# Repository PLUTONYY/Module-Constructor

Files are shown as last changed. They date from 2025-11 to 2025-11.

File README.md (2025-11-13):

# Module-Constructor
##  Назначение системы

Узел полезной нагрузки представляет собой модульное универсальное устройство, позволяющее решать задачи по:

- Обнаружению грузов переноски и дефектов ЛЭП;
- Переключению камер для удобства управления;
- Переноске грузов разных типов;
- Очистке ЛЭП;
- Индикации состояния.

---

## Инструкция для сборки модуля

1. Распечатайте все `.plgx` файлы на 3D-принтере.  
2. Соберите конструкцию в соответствии со схемой сборки, используя стяжки и термоклей.  
3. Проверьте конструкцию модулей на наличие жёсткой фиксации всех компонентов.  
4. Соберите электрическую часть модулей в соответствии со схемой электрических соединений.  
5. Проверьте электрическую схему на наличие короткого замыкания и правильность соединения проводов.

---

## Инструкция для развертывания системы

1. Подсоедините полётный контроллер к компьютеру.  
2. Откройте **Betaflight App** и подключитесь к дрону.  
3. Зайдите на вкладку **«Предустановки»** и выберите **«Загрузить резервную копию»**.  
4. Выберите файл `Constructor_bf.txt` и загрузите его в полётный контроллер.  
5. Подключите аппаратуру управления к компьютеру.  
6. Выберите режим **«USB Storage (SD)»**, после чего появится подключение на ПК.  
7. Откройте папку **`MODELS`** и переместите в неё файл `Constructor_rx.txt`.

---

### Примечание
Перед первым запуском рекомендуется проверить все соединения и убедиться в правильности конфигурации полётного контроллера.
ссылка на яндекс диск с презентацией и видео
https://disk.yandex.ru/d/g-EM2BR4wADh5Q

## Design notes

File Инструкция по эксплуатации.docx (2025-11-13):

# Назначение системы

Узел полезной нагрузки представляет из себя модульное универсальное устройство, позволяющее решать задачи по:

- Обнаружению грузов переноски и дефектов ЛЭП;
- Переключению камер для удобства управления;
- Переноске грузов разных типов;
- Очистке ЛЭП;
- Индикации состояния.

Инструкция для сборки модуля

1. Распечатайте все stl файлы на 3д- принетере
2. Соберите конструкцию в соответствии со схемой сборки, используя стяжки и термоклей
3. Проверите консрукцию модулей на наличие жесткой фиксации всех компонентов.
4. Соберите электрическую часть модулей в соответствии со схемой электрических соединение
5. Проверите электрическую схему на наличие короткого замыкания и правильности соединения проводов.

Инструкция для развертывания системы

1. Подсоедините полетный контроллер к компьютеру.
2. Откройте Betaflight App (https://app.betaflight.com/) и подключитесь к дрону

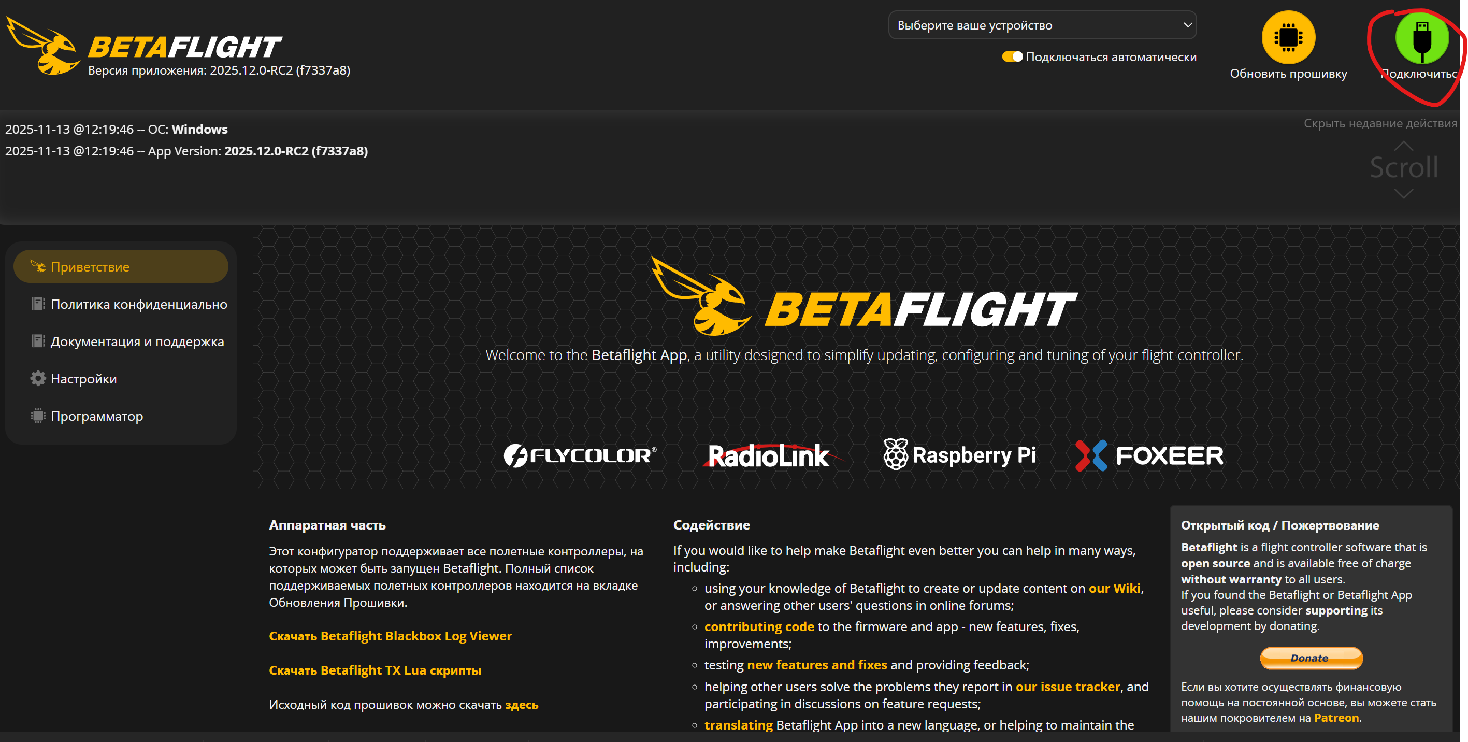
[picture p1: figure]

3. Зайдите на вкладку «Предустановки» и Выберите «Загрузить резервную копию»

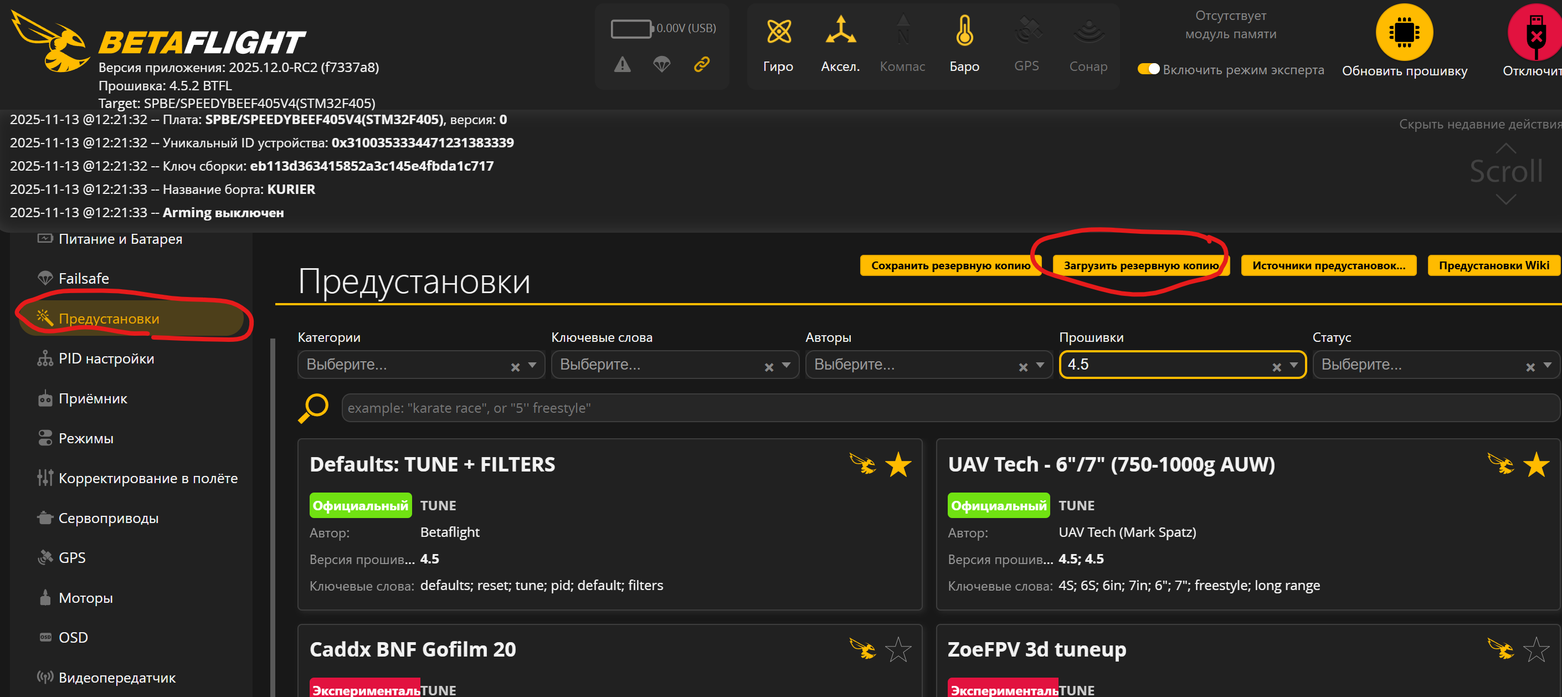
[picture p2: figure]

4. Выберите файл «Constructor_bf.txt» и загрузите в полетный контроллер
5. Подключите аппаратуру управления к компьютеру
6. Выберите режим «USB Storage (SD)» после чего появится подключение на ПК
7. Окройте папку «MODELS» и переместите в нее файл «Constructor_rx.txt»

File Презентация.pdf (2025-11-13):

# Модуль для очистки ЛЭП и переноса грузов «Консруктор»

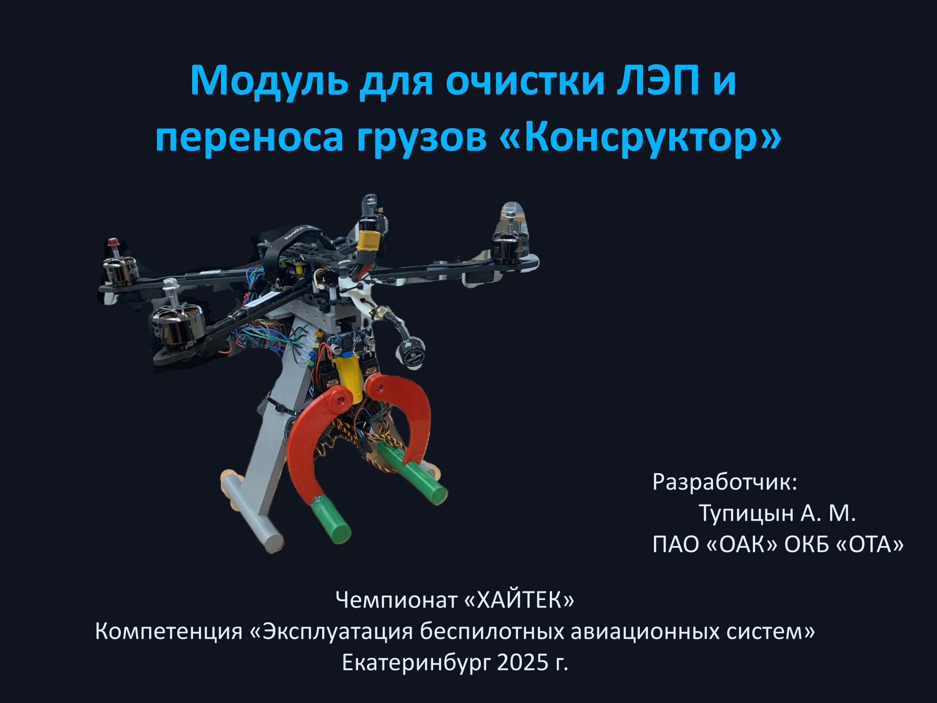
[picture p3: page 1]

Чемпионат «ХАЙТЕК»
Компетенция «Эксплуатация беспилотных авиационных систем» Екатеринбург 2025 г.

Разработчик:
Тупицын А. М.
ПАО «ОАК» ОКБ «ОТА»

# Описание модуля

Универсальный подвесной модуль для БПЛА малого класса:
- Обнаружению грузов переноски и дефектов ЛЭП;
- Переключению камер для удобства управления;
- Переноске грузов разных типов;
- Очистке ЛЭП;
- Индикации состояния.

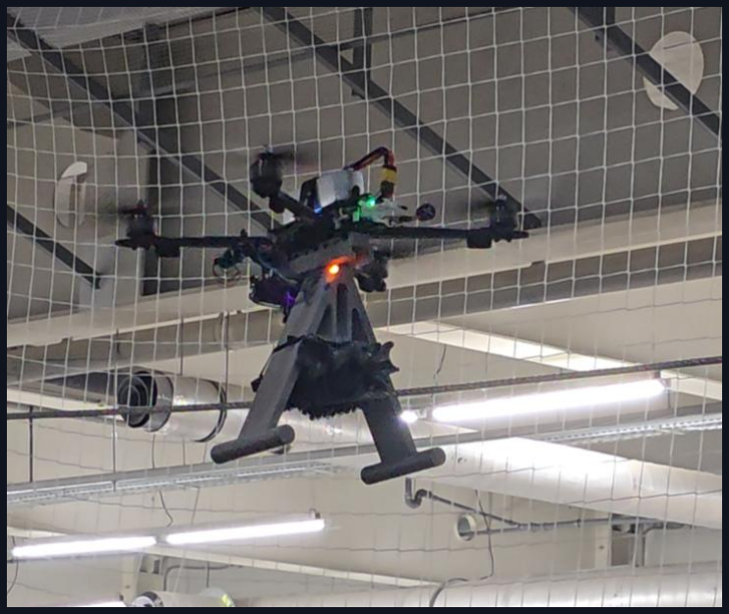
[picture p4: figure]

- Очистка ЛЭП от наледи

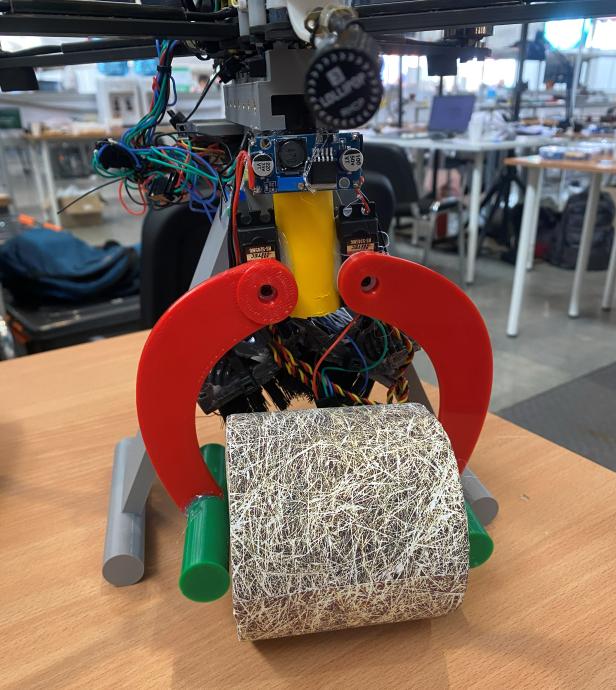
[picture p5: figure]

и загрязнений | • Перенос грузов до 500 гр

# Используемые комплектующие

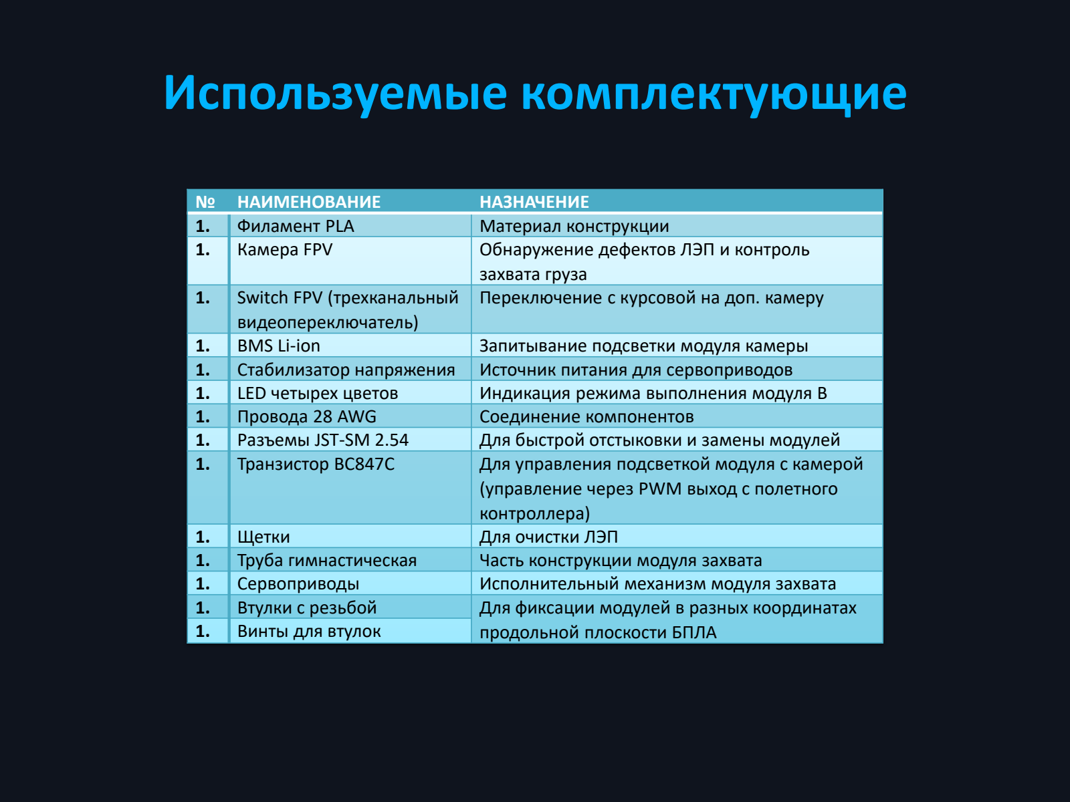
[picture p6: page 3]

№ | НАИМЕНОВАНИЕ | НАЗНАЧЕНИЕ
1. | Филамент PLA | Материал конструкции
1. | Камера FPV | Обнаружение дефектов ЛЭП и контроль захвата груза
1. Switch FPV (трехканальный | видеопереключатель) | Переключение с курсовой на доп. камеру
1. | BMS Li-ion | Запитывание подсветки модуля камеры
1. | Стабилизатор напряжения | Источник питания для сервоприводов
1. | LED четырех цветов | Индикация режима выполнения модуля B
1. | Провода 28 AWG | Соединение компонентов
1. | Разъемы JST-SM 2.54 | Для быстрой отстыковки и замены модулей
1. | Транзистор BC847C | Для управления подсветкой модуля с камерой (управление через PWM выход с полетного контроллера)
1. | Щетки | Для очистки ЛЭП
1. | Труба гимнастическая | Часть конструкции модуля захвата
1. | Сервоприводы | Исполнительный механизм модуля захвата
1. | Втулки с резьбой | Для фиксации модулей в разных координатах продольной плоскости БПЛА
1. | Винты для втулок

# Испытания по переносу грузов

- БПЛА: грузоподъёмность 800 г
- Груз: до 500 г
Итог: БПЛА не взлетел из-за технических неполадок

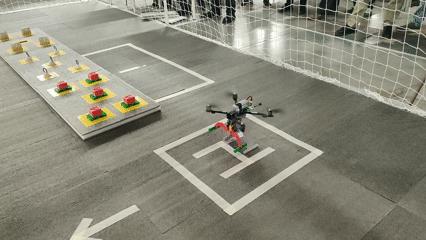
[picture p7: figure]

# Испытания по очистке ЛЭП

- Участок: ЛЭП 20м
- Эффективность очистки: 20%
- Время 100 м линии: 10 мин
Итог:
- Зачистка одного участка загрязнений
- Крушение из-за столкновением с проводом

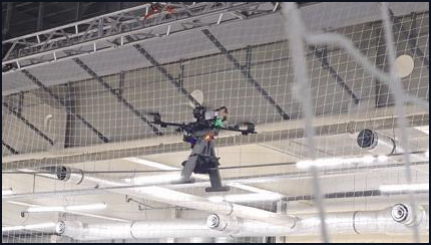
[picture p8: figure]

# Экономическое обоснование

Себестоимость:
- Модуль: 10 000₽
- БПЛА : 100 000₽
Затраты на вылет:
- Оплата услуг оператора БПЛА: 100 000₽
- Запасные комплектующие: 5 000₽ Прибыль:
- Очистка 1 км ЛЭП вручную: 250 000 ₽ Окупаемость ~ 2 месяца

Преимущества разработки:
- Снижение затрат и рисков
- Повышение безопасности работ
- Быстрое развертывание
- Модульная совместимость с разными БПЛА

# Перспективы развития

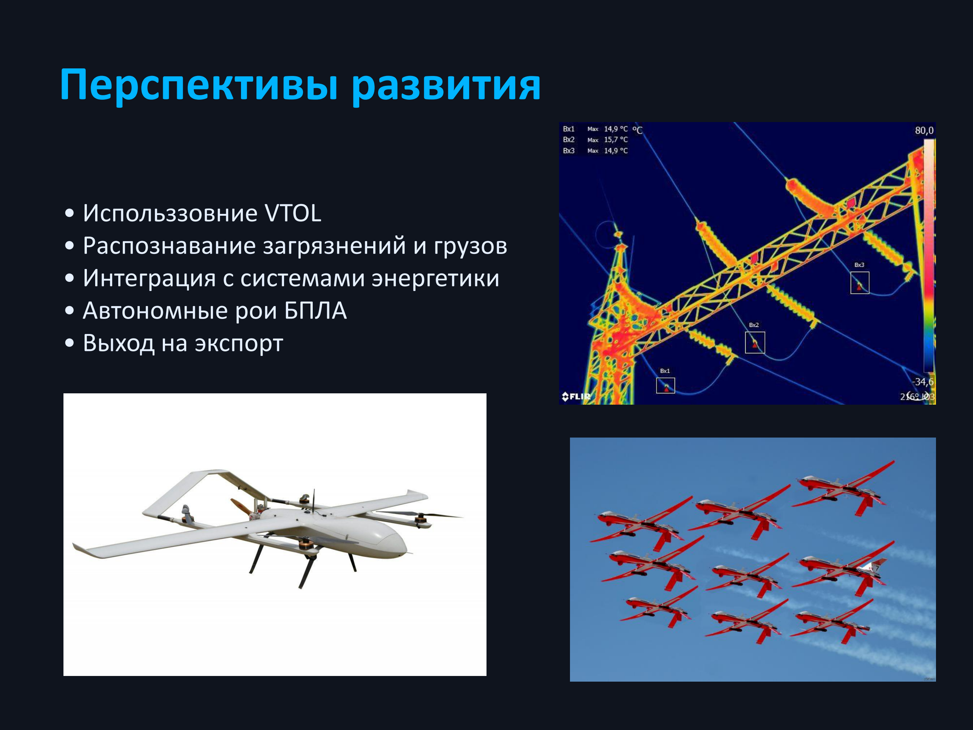
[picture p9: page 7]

- Использзовние VTOL
- Распознавание загрязнений и грузов
- Интеграция с системами энергетики
- Автономные рои БПЛА
- Выход на экспорт

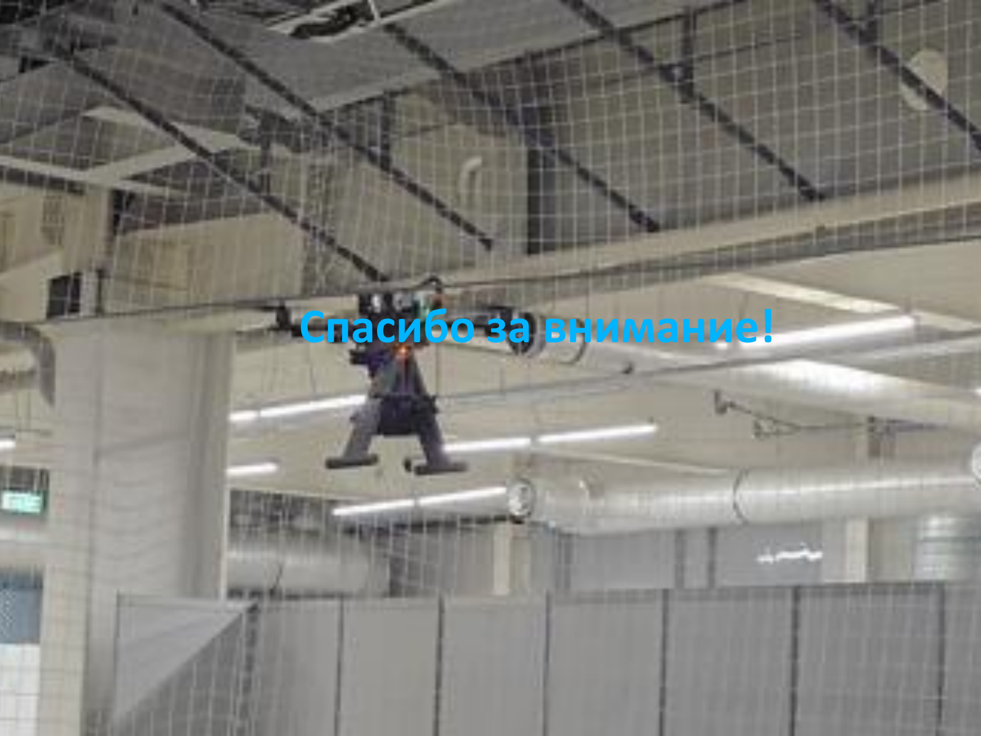
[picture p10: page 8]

# Спасибо за внимание!

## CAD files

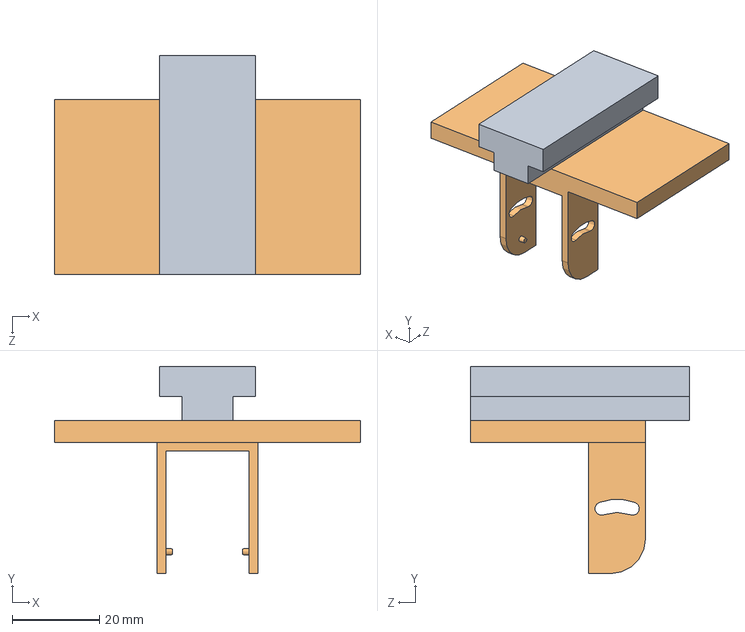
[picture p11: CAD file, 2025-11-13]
Модель сборки/Assem Cam.SLDASM
70.0 x 47.4 x 50.0 mm
inner rail for wire checker
Cam bracket

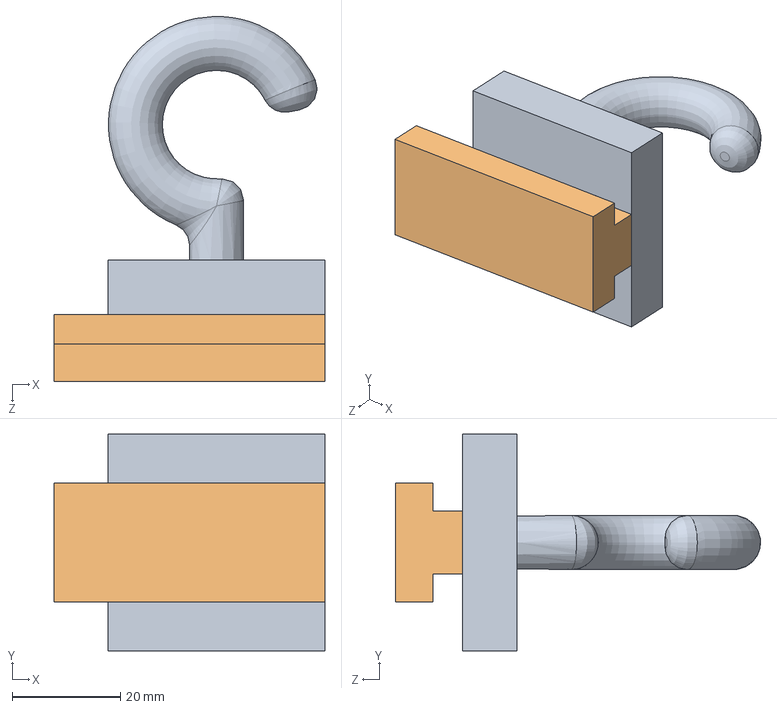
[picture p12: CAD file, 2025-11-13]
Модель сборки/Assem Hook.SLDASM
50.0 x 40.0 x 67.3 mm
Hook
inner rail for wire checker

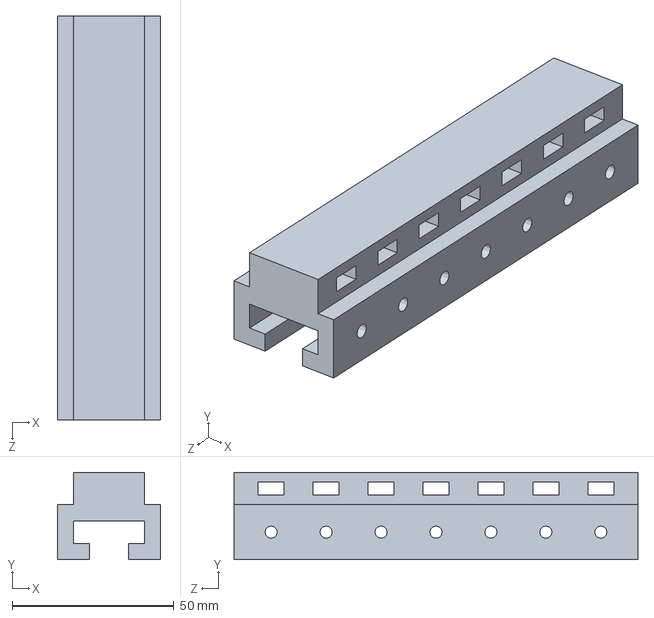
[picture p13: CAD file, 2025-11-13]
Модель сборки/Main rail_clear.SLDPRT
32.0 x 27.0 x 125.0 mm

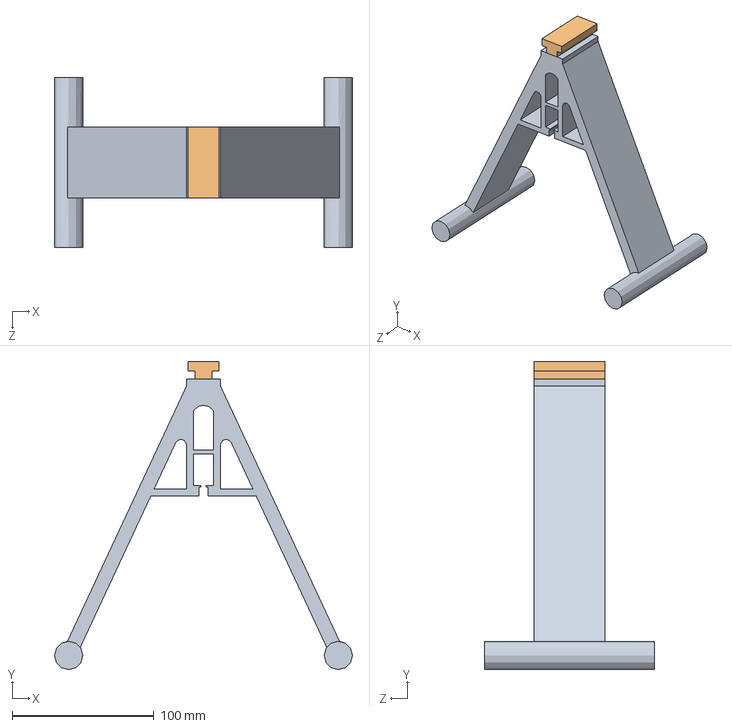
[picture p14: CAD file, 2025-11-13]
Модель сборки/Assem Wire Checker.SLDASM
210.2 x 217.4 x 120.0 mm
Wire Checker
inner rail for wire checker

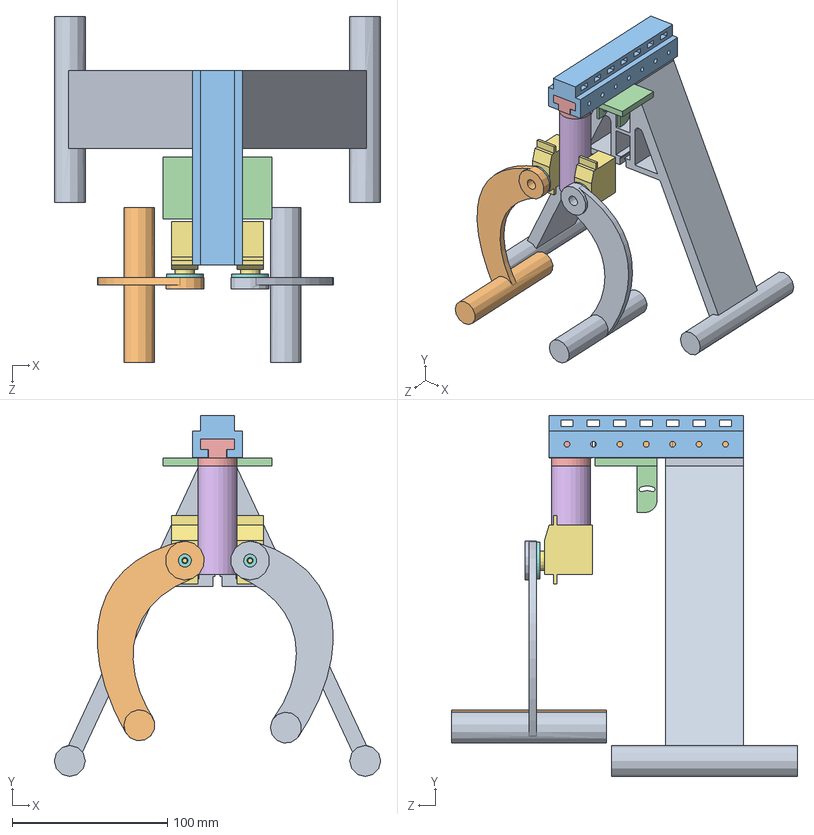
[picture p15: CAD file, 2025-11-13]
Модель сборки/Assem claw.SLDASM
210.2 x 232.4 x 223.0 mm
Wire Checker
inner rail for wire checker x 2
Main rail_clear
Cam bracket
Top of catcher
tube
Servo x 2
Servo's disk x 2
Claw_Mirrored
Claw

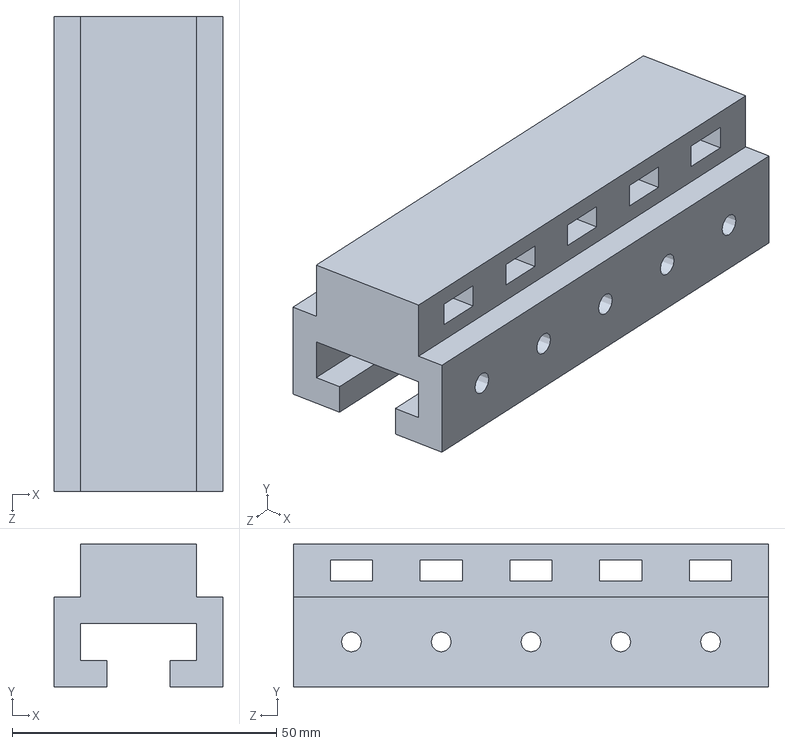
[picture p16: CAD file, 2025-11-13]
Модель сборки/Main rail.SLDPRT
32.0 x 27.0 x 90.0 mm

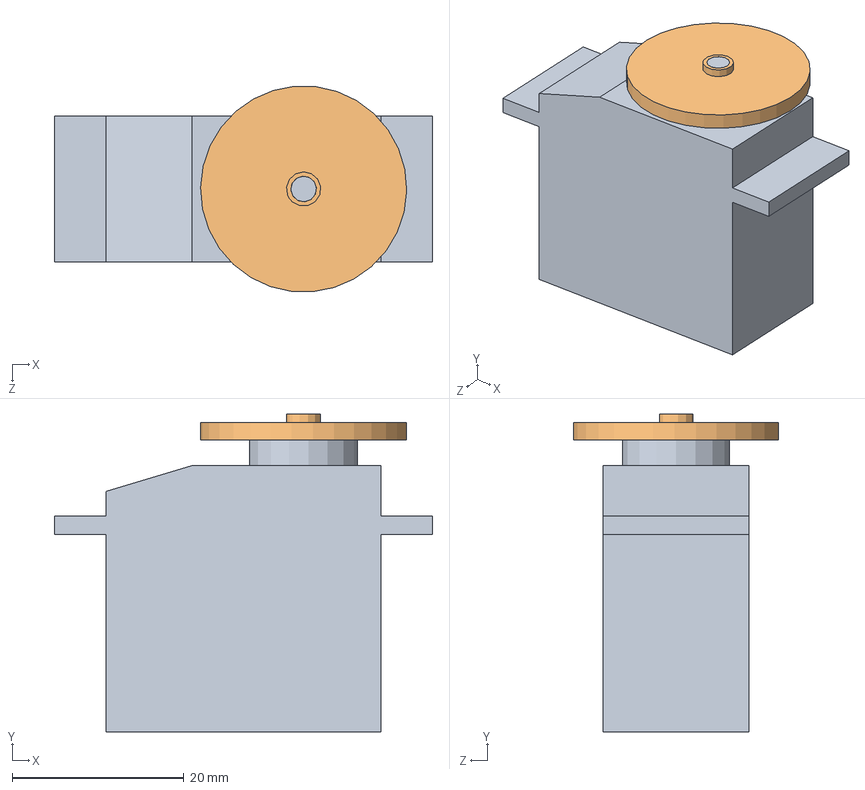
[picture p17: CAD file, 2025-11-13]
Модель сборки/Servo_assem.SLDASM
44.0 x 37.0 x 23.9 mm
Servo
Servo's disk

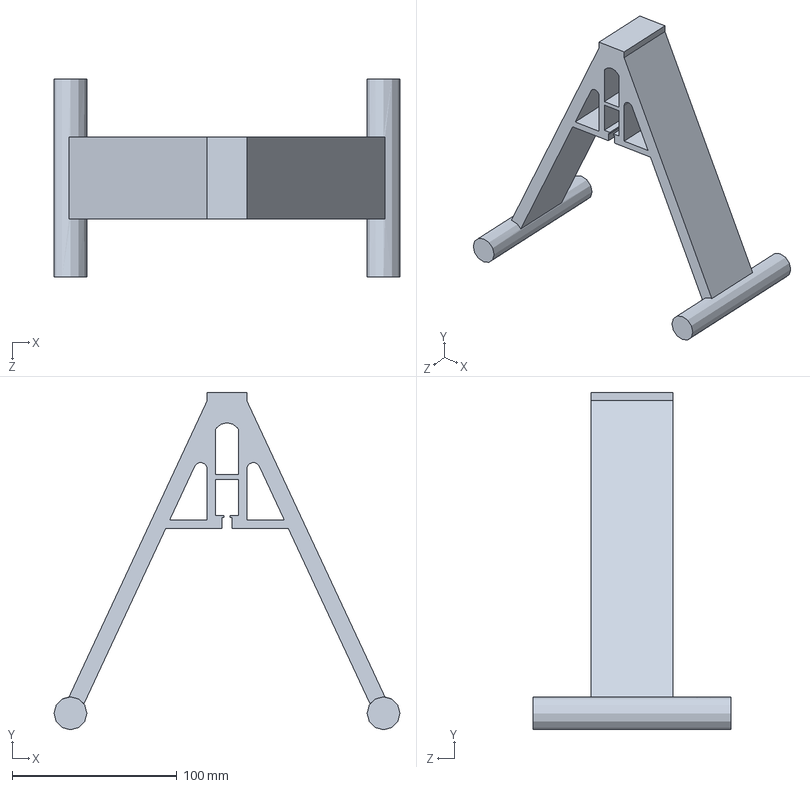
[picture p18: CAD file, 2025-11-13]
Модель сборки/Wire Checker.SLDPRT
210.2 x 205.0 x 120.0 mm

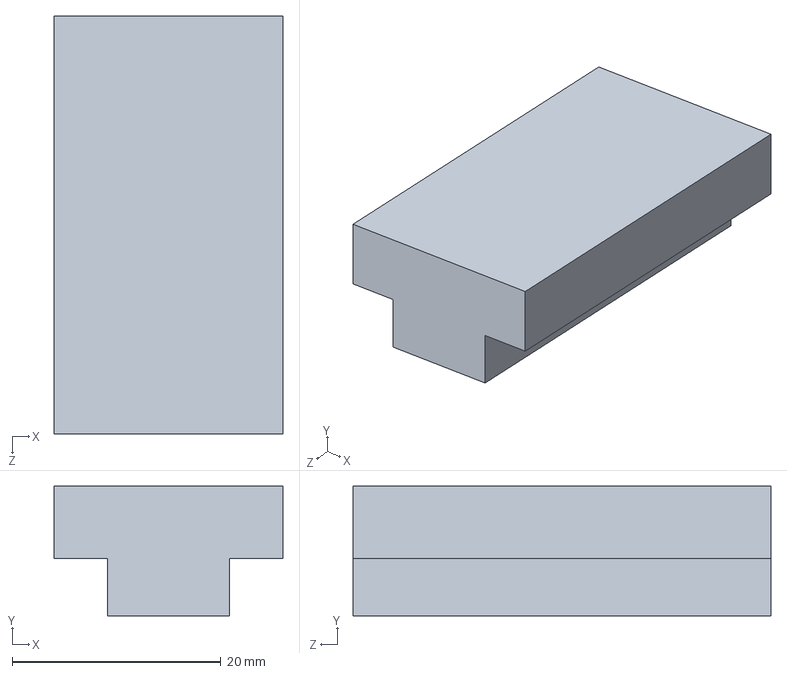
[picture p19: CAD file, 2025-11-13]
Модель сборки/inner rail test.SLDPRT
21.9 x 12.4 x 40.0 mm

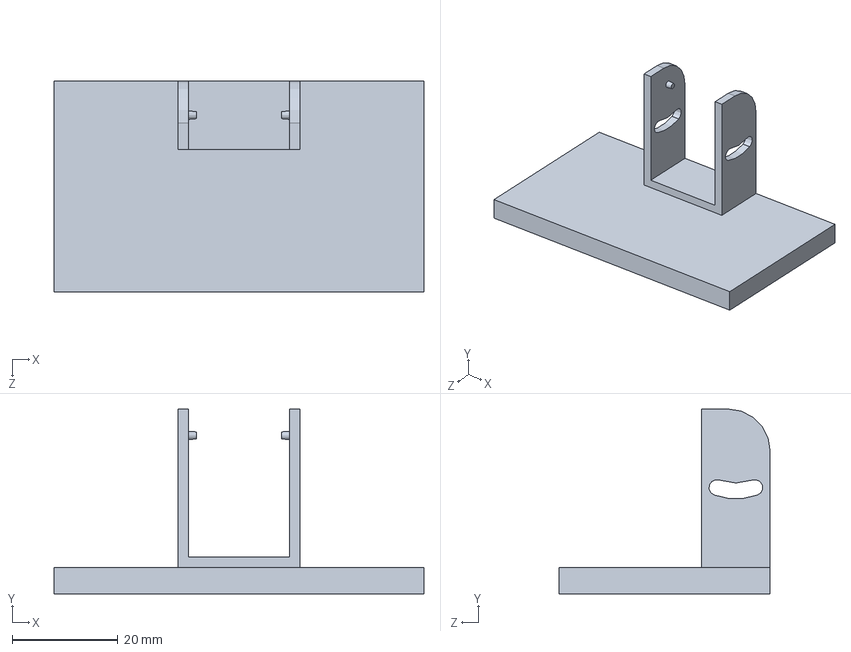
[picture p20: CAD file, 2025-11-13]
Модель сборки/Cam bracket.SLDPRT
70.0 x 35.0 x 40.0 mm

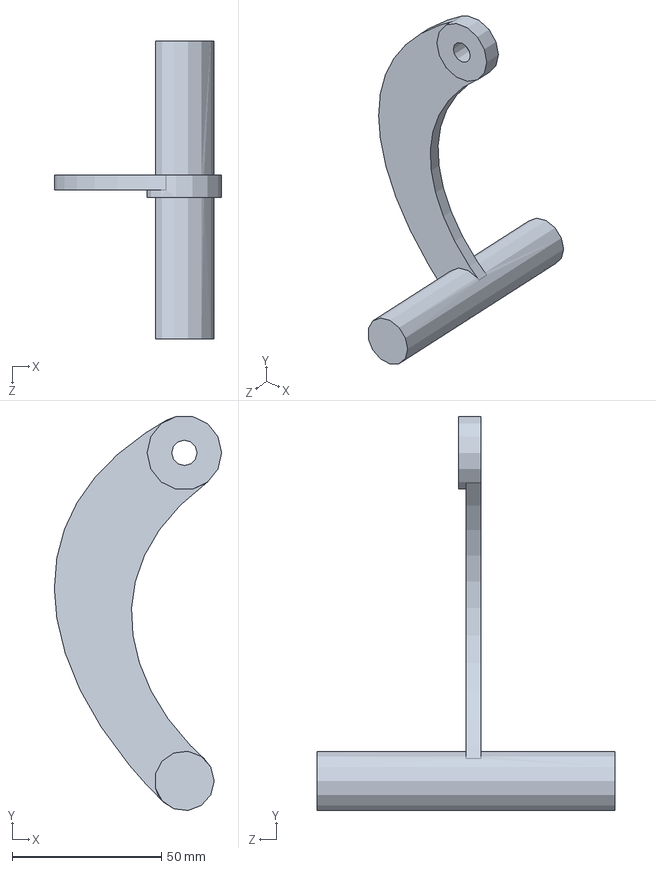
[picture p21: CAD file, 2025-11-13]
Модель сборки/Claw.SLDPRT
56.1 x 132.1 x 100.0 mm

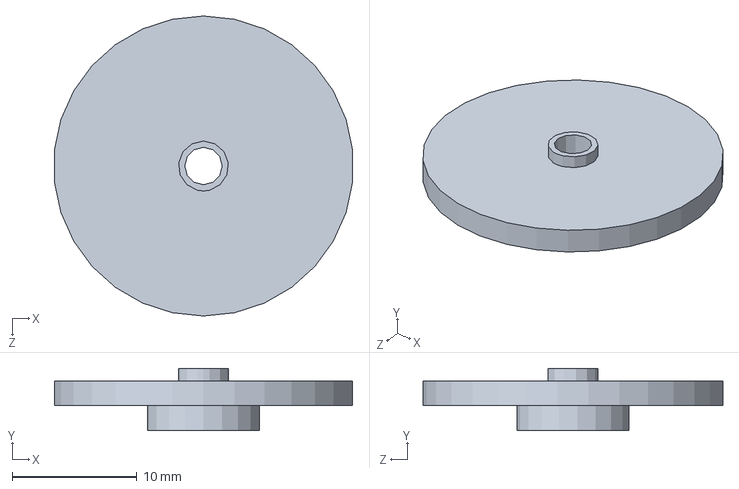
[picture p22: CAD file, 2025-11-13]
Модель сборки/Servo's disk.SLDPRT
23.9 x 5.00 x 24.0 mm

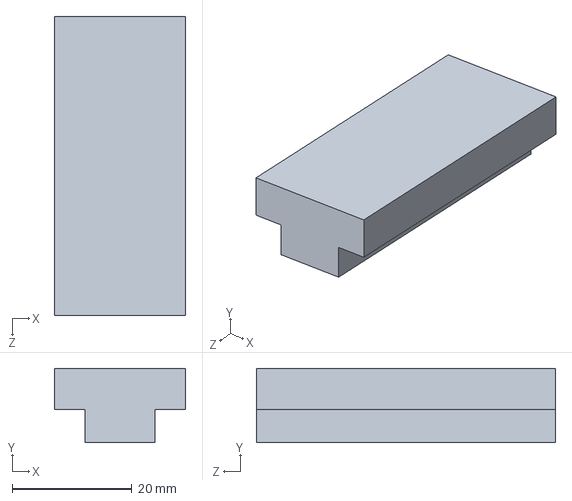
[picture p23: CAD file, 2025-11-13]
Модель сборки/inner rail for wire checker.SLDPRT
21.9 x 12.4 x 50.0 mm

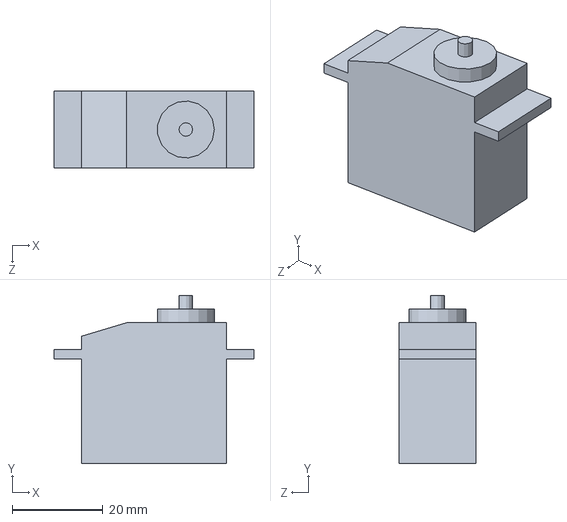
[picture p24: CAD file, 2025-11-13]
Модель сборки/Servo.SLDPRT
44.0 x 37.0 x 17.0 mm

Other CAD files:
Чертежи/AUTOCAD/Общий вид.dwg
Чертежи/AUTOCAD/Структурная схема.dwg
Модель сборки/Part1.SLDPRT
Модель сборки/Top of catcher.SLDPRT
Модель сборки/Assem claw/Assem claw/Assem Cam.iam
Модель сборки/Assem claw/Assem claw/Assem Wire Checker.iam
Модель сборки/Assem claw/Assem claw/Assem claw.iam
Модель сборки/Assem claw/Assem claw/Cam bracket.ipt
Модель сборки/Assem claw/Assem claw/Claw.ipt
Модель сборки/Assem claw/Assem claw/Claw_Mirrored.ipt
Модель сборки/Assem claw/Assem claw/Main rail_clear.ipt
Модель сборки/Assem claw/Assem claw/Servo's disk.ipt
Модель сборки/Assem claw/Assem claw/Servo.ipt
Модель сборки/Assem claw/Assem claw/Servo_assem.iam
Модель сборки/Assem claw/Assem claw/Top of catcher.ipt
Модель сборки/Assem claw/Assem claw/Wire Checker.ipt
Модель сборки/Assem claw/Assem claw/inner rail for wire checker.ipt
Модель сборки/Assem claw/Assem claw/tube.ipt
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

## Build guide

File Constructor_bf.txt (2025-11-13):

defaults nosave

# version
# Betaflight / STM32F405 (S405) 4.5.2 Nov  9 2025 / 13:51:33 (024f8e13d) MSP API: 1.46
# config rev: a3507b7

# start the command batch
batch start

# reset configuration to default settings
defaults nosave

board_name SPEEDYBEEF405V4
manufacturer_id SPBE
mcu_id 0039001e3133471834333035
signature 

# resources
resource MOTOR 5 NONE
resource MOTOR 6 NONE
resource MOTOR 7 NONE
resource MOTOR 8 NONE
resource SERVO 1 B10
resource SERVO 2 A15
resource SERVO 3 C08
resource SERVO 4 C09
resource SERIAL_TX 6 NONE
resource SERIAL_RX 1 NONE
resource SERIAL_RX 6 NONE
resource PINIO 1 A10
resource PINIO 2 C07
resource PINIO 3 C06

# feature
feature SERVO_TILT
feature TELEMETRY
feature LED_STRIP
feature DISPLAY
feature OSD
feature CHANNEL_FORWARDING

# master
set osd_canvas_height = 13
set pinio_config = 129,129,129,129
set pinio_box = 40,41,42,43

profile 0

profile 1

profile 2

profile 3

# restore original profile selection
profile 0

rateprofile 0

rateprofile 1

rateprofile 2

rateprofile 3

# restore original rateprofile selection
rateprofile 0

# save configuration

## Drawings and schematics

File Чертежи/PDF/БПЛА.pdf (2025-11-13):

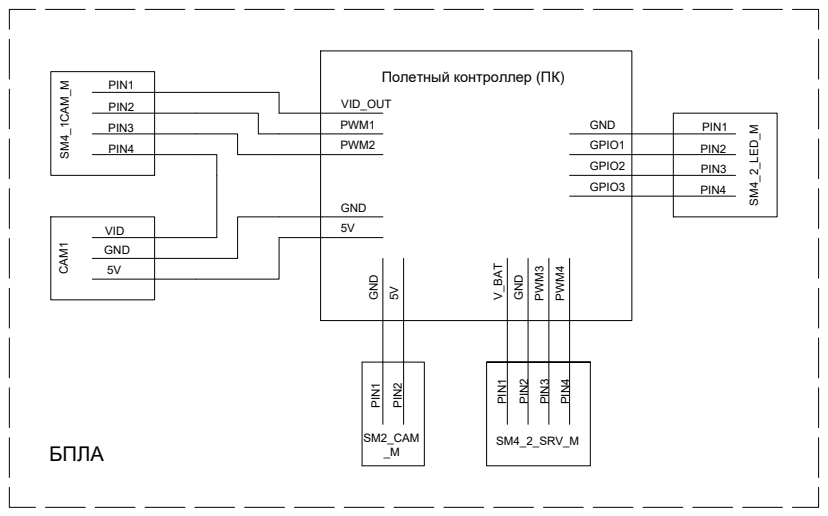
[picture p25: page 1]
PWM4 GND GPIO1 GPIO2 GPIO3; 5V PIN2 PIN3 PIN4 PIN1; PIN4 PIN2 PIN3 PIN4 PIN1 SM4_2_LED_M SM2_CAM SM4_2_SRV_M _M GND 5V; CAM1 БПЛАGND 5VVID

Полетный контроллер (ПК) VID_OUT PWM1 PWM2

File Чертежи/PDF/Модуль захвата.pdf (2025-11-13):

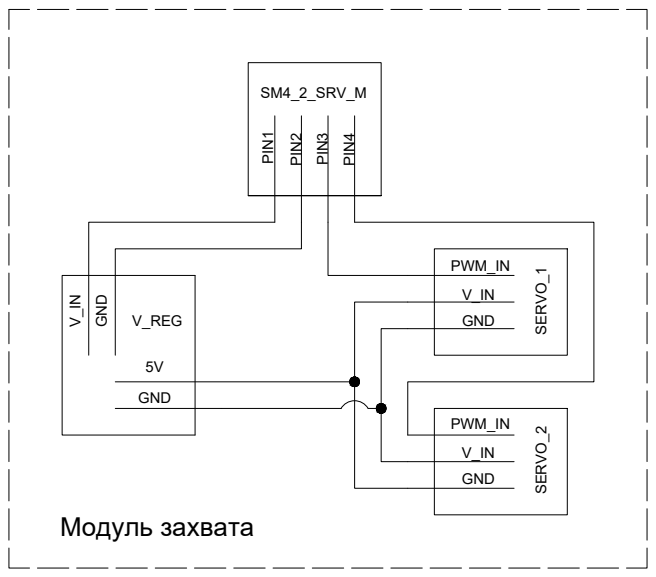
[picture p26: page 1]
PIN4 SM4_2_SRV_M; SERVO_1 SERVO_2 V_REG V_IN GND PWM_IN GND 5V

GND V_IN GND PWM_IN Модуль захвата

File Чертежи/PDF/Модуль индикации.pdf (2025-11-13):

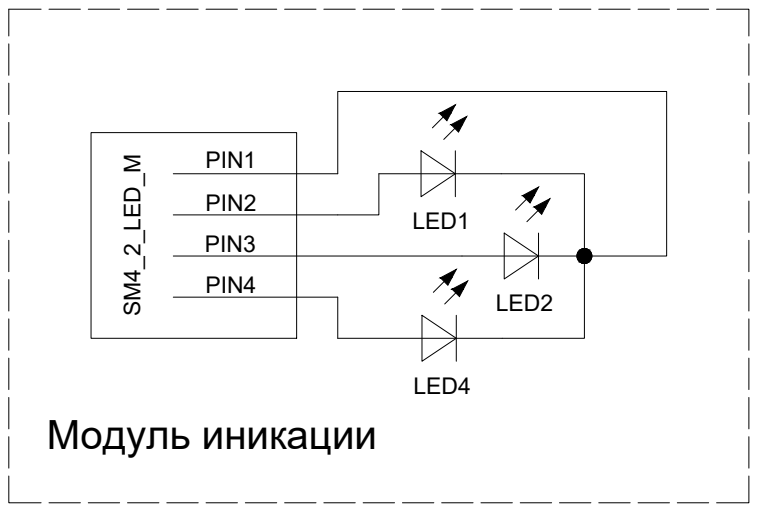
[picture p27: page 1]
PIN2 PIN3 PIN4 PIN1 SM4_2_LED_M LED1 LED2 LED4 Модуль иникации

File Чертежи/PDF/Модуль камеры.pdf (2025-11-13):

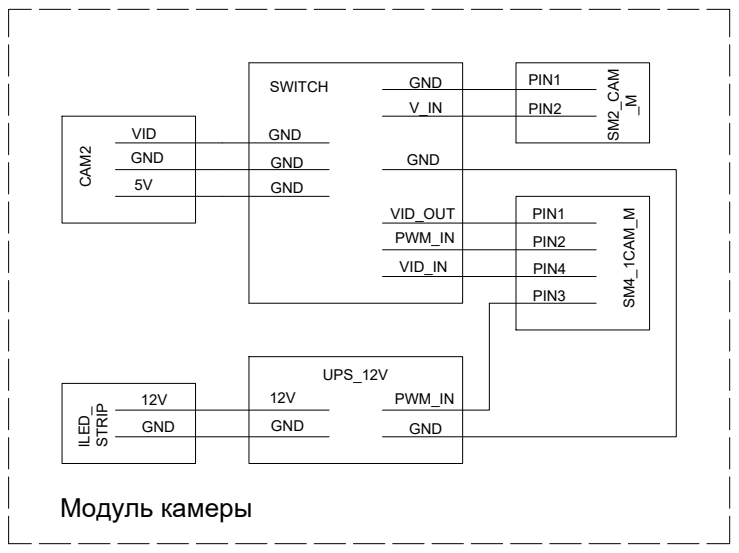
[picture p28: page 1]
PIN2 PIN1 _M PIN2 PIN4 PIN3 PIN1; SM4_1CAM_M SWITCH; CAM2GND 5VVID UPS_12V

STRIP12V GND 12V GND PWM_IN GND GND GND GND V_IN VID_OUT PWM_IN VID_IN GND GND Модуль камеры

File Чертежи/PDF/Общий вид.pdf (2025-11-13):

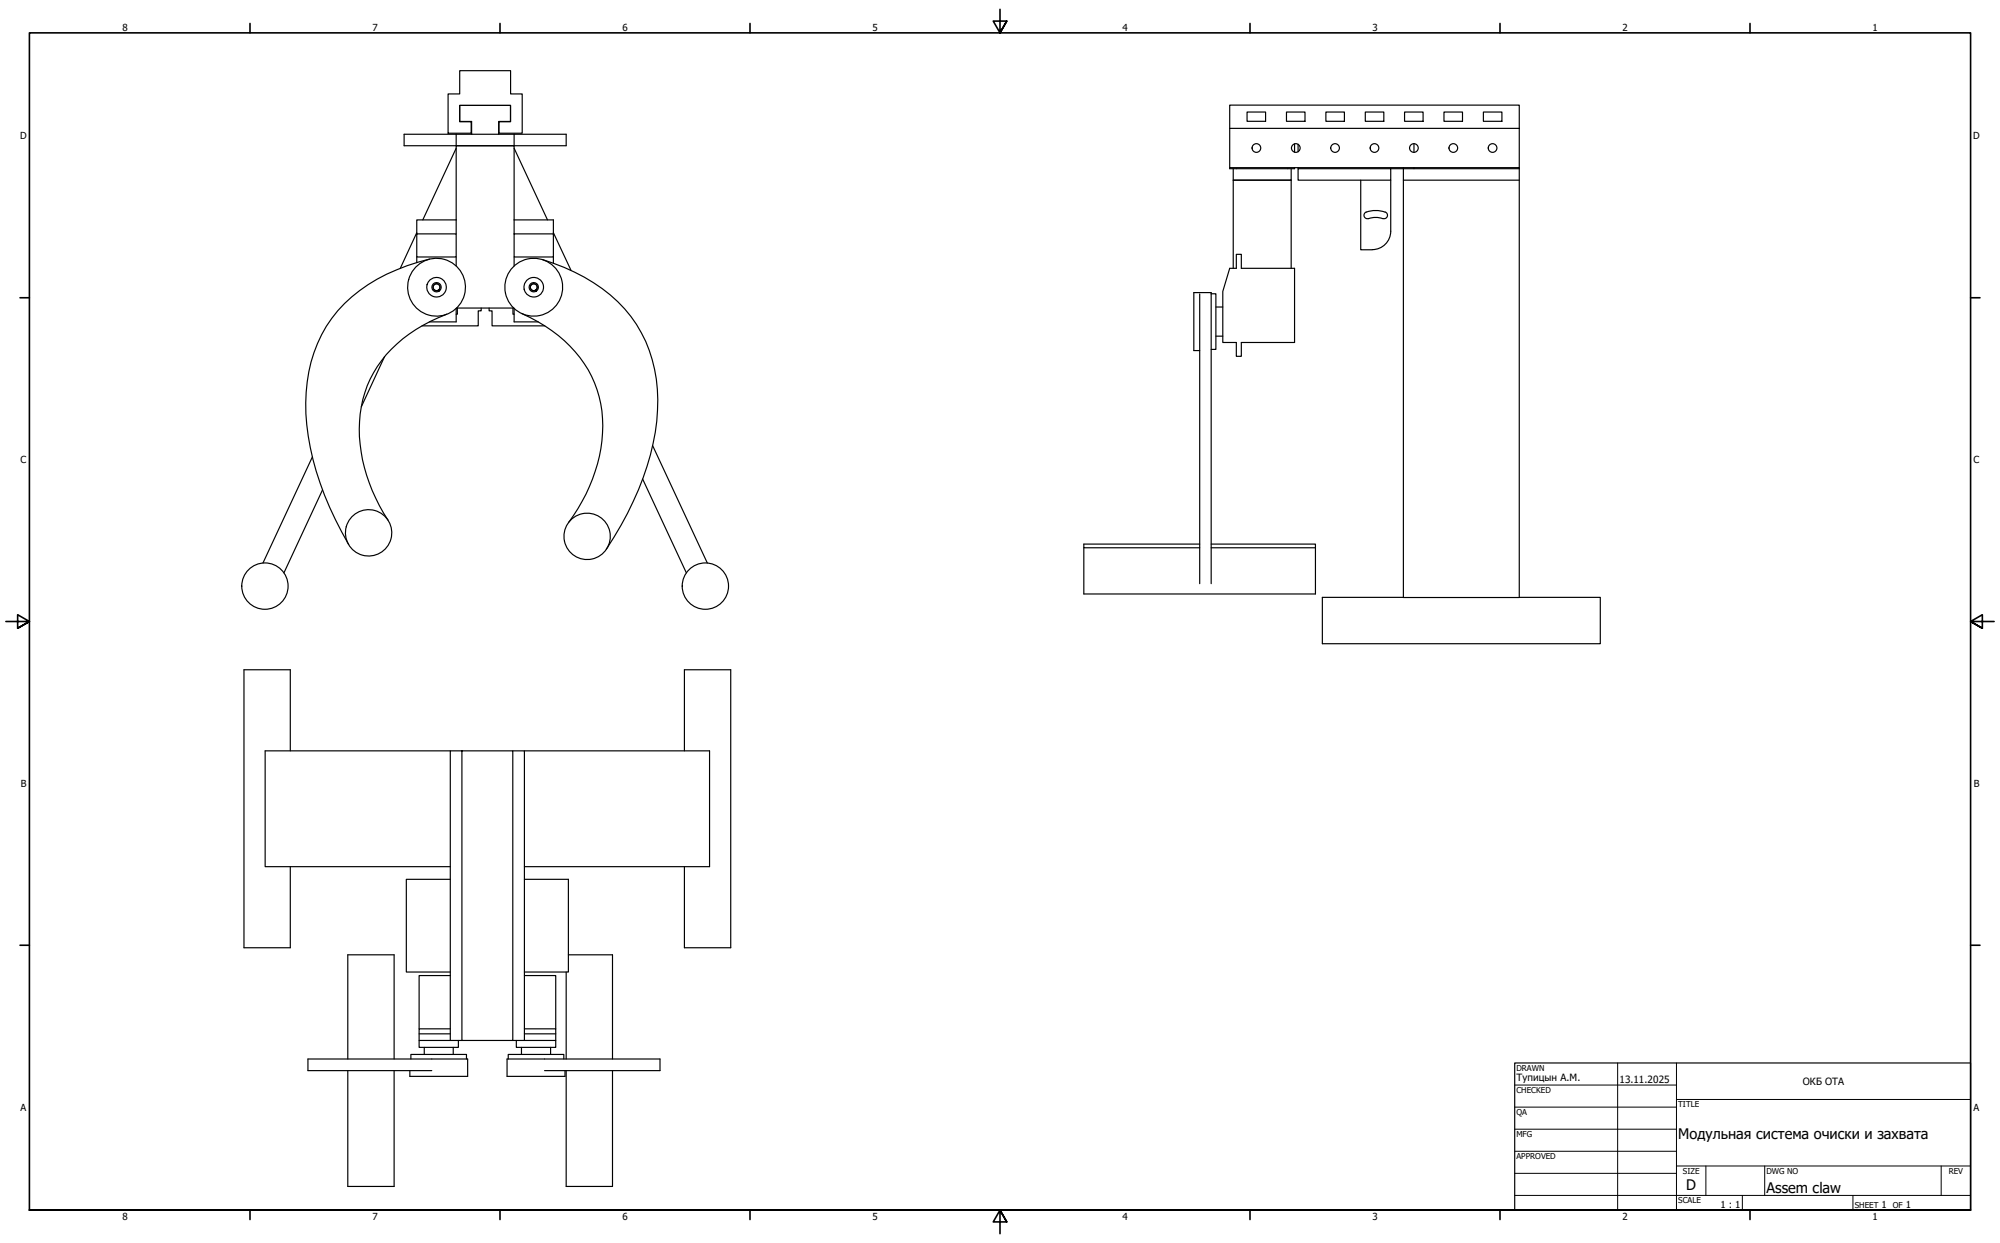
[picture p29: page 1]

DRAWN Тупицын А.М. | 13.11.2025 | ОКБ ОТА

CHECKED

TITLE
Модульная система очиски и захвата

MFG

APPROVED

SIZE D | DWG NO Assem claw | REV

SCALE 1 : 1 | | SHEET 1 OF 1

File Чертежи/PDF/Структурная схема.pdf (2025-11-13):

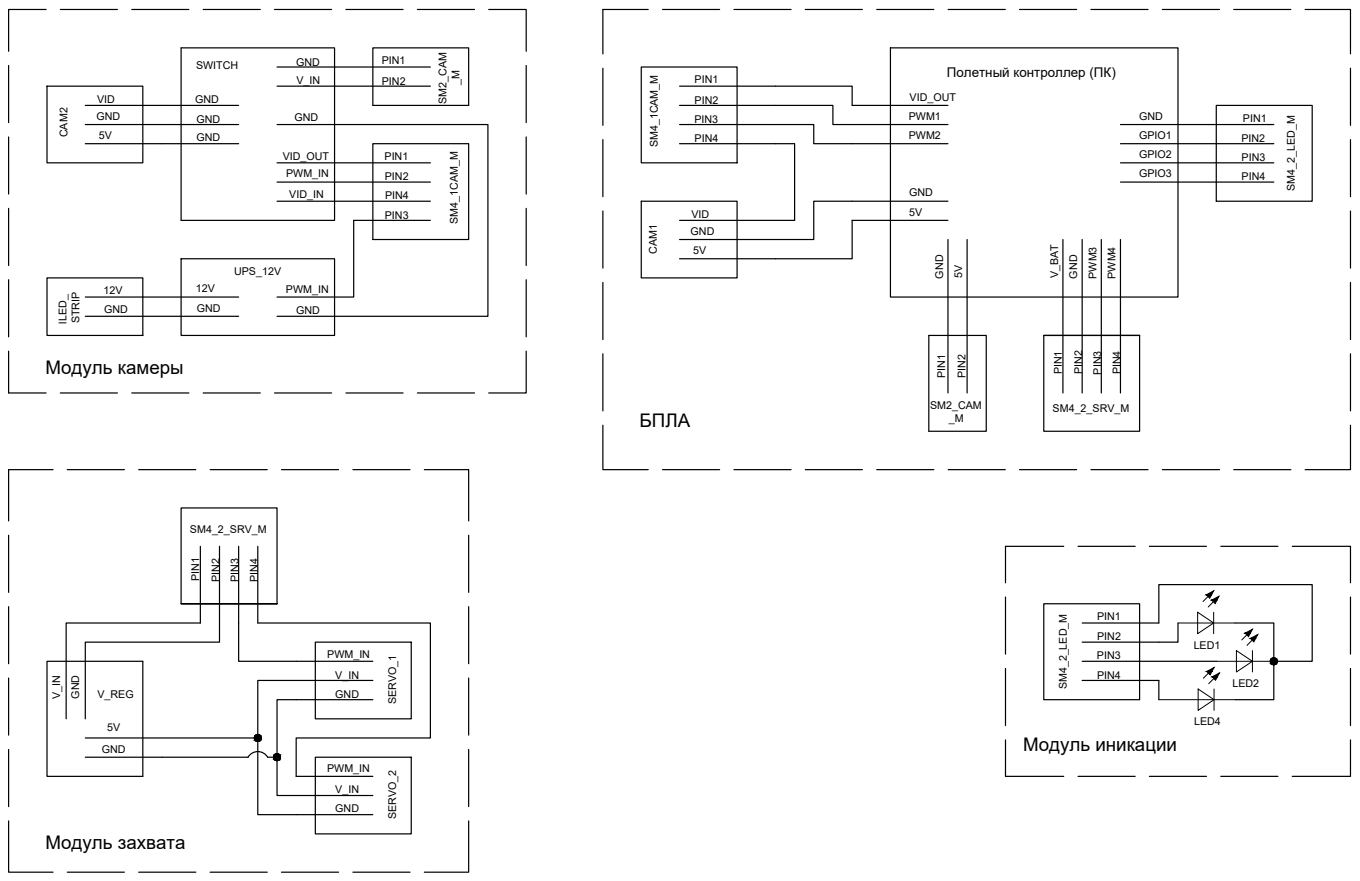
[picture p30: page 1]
PWM4 GND GPIO1 GPIO2 GPIO3; 5V PIN2 PIN3 PIN4 PIN1; PIN4 PIN2 PIN3 PIN4 PIN1 SM4_2_LED_M SM2_CAM SM4_2_SRV_M _M GND 5V; CAM1 БПЛА PIN2 PIN3 PIN4 PIN1; SM4_2_LED_M LED1 LED2 LED4 Модуль иникации PIN2 PIN1 _M PIN2 PIN4 PIN3 PIN1; SM4_1CAM_M SWITCH GND 5VVID; CAM2GND 5VVID UPS_12V; PIN4 SM4_2_SRV_M; SERVO_1 SERVO_2 V_REG V_IN GND PWM_IN GND 5V

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

Полетный контроллер (ПК) VID_OUT PWM1 PWM2

GND V_IN GND PWM_IN Модуль захвата
